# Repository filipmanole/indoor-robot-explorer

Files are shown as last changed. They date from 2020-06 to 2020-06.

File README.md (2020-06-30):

<!-- PROJECT SHIELDS -->
<!--
*** I'm using markdown "reference style" links for readability.
*** Reference links are enclosed in brackets [ ] instead of parentheses ( ).
*** See the bottom of this document for the declaration of the reference variables
*** for contributors-url, forks-url, etc. This is an optional, concise syntax you may use.
*** https://www.markdownguide.org/basic-syntax/#reference-style-links
-->

[][contributors-url]
[][forks-url]
[][stars-url]
[][issues-url]
[][linkedin-url]

<!-- PROJECT LOGO -->
<br />
<p align="center">

  <h1 align="center">Indoor Robot Explorer</h1>

  <p align="center">
    <a href="https://github.com/filipmanole/indoor-robot-explorer/issues">Report Bug</a>
    ·
    <a href="https://github.com/filipmanole/indoor-robot-explorer/issues">Request Feature</a>
  </p>
</p>

<!-- TABLE OF CONTENTS -->

## Table of Contents

- [About the Project](#about-the-project)
- [Software Tools](#software-tools)
- [Hardware](#hardware)
- [Getting Started](#getting-started)
  - [Prerequisites](#prerequisites)
  - [Usage](#usage)
- [Roadmap](#roadmap)
- [Contributing](#contributing)
- [License](#license)

<!-- ABOUT THE PROJECT -->

## About The Project

In recent years there has been an increase in interest in robots. There are billions of dollar spent on professional and personal use robots: autonomous vehicles, maintenance robots, cleaning robots. This repository offers a well structured, modular and low cost robot.

## Software Tools

Board layout was designed using [EAGLE 9.2.2](https://www.autodesk.com/products/eagle/overview?plc=F360&term=1-YEAR&support=ADVANCED&quantity=1)

Firmware was developed using:
- [MPLAB X 5.30](https://www.microchip.com/mplab/mplab-x-ide)
- dsPIC33E-GM-GP-MC-GU-MU_DFP 1.0.23
- [XC16](https://www.microchip.com/mplab/compilers) v1.50

Raspberry Pi specifications:
- [Raspbian GNU/Linux 9 (stretch)](https://www.raspberrypi.org/downloads/raspberry-pi-os/)
- [GCC](https://gcc.gnu.org/) version 6.3.0
- Python 2.7

## Hardware

### Main Components Used
- LiPo Battery 7V4 2200mA
- [dsPIC33EP128GM304](https://www.microchip.com/wwwproducts/en/dsPIC33EP128GM304) microcontroller
- 2x [MC33926](https://www.nxp.com/docs/en/data-sheet/MC33926.pdf) Motor Drivers
- 2x [Pololu ](https://www.pololu.com/product/2283) DC Motors
- 3x [VL53L0X]() Time of Flight Sensors
- [Raspberry Pi Zero W](https://www.raspberrypi.org/products/raspberry-pi-zero-w/)

In the `eagle_project` directory can be found the schematic, the layout design of the board and the Bill of Material. Those files can be used to send the board to manufacture and build the robot. You should obtain something like:

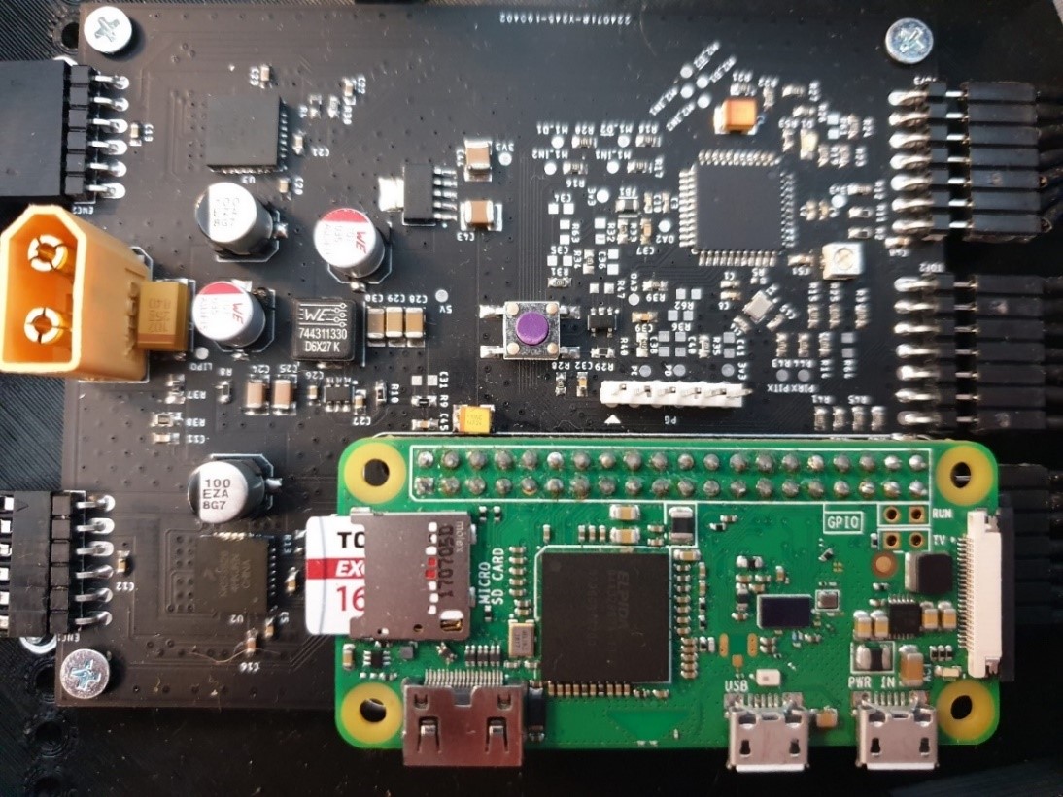
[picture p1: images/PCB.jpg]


<!-- GETTING STARTED -->

## Getting Started

To get a local copy up and running follow these simple example steps.

### Prerequisites

Make sure you have the following:
- The tools specified in [Software Tools](#software-tools) section
- The robot obtained from the files in the `eagle_project` directory
- [PICkit™ 3](https://www.microchip.com/DevelopmentTools/ProductDetails/PG164130) to programm the robot
- `ssh` connection to the Raspberry Pi Zero W.

```sh
git clone https://github.com/filipmanole/indoor-robot-explorer.git
```

<!-- USAGE EXAMPLES -->

### Usage

Program the robot:
1. Open the MPLAB X project `driver.X`
2. Right click on the project and select `Build`
3. Program the robot using the PICkit 3

Copy the directory `robot-utils` on the Raspberry Pi:
```sh
scp robot-utils/ pi_user@raspberry_pi_address:~
```
Log on the Raspberry Pi:
```sh
ssh pi_user@raspberry_pi_address
```
Run commands to move the robots:
```sh
cd ~/robot-utils/commands
make build
robot start        # robot can be controlled now
robot run 0.3 0.1  # first argument is the linear velocity, the second is the angular velocity
robot pose         # returns the position of the robot x, y and tetha
robot stop         # the robot stops
```

Example of how to get data from the sensors:
```sh
cd ~/robot-utils/tof/VL53L0X
python VL53L0X_multi_example.py
```

<!-- ROADMAP -->

## Roadmap

See the [open issues](https://github.com/filipmanole/indoor-robot-explorer/issues) for a list of proposed features (and known issues).

<!-- CONTRIBUTING -->

## Contributing

Contributions are what make the open source community such an amazing place to be learn, inspire, and create. Any contributions you make are **greatly appreciated**.

1. Fork the Project
2. Create your Feature Branch (`git checkout -b feature/AmazingFeature`)
3. Commit your Changes (`git commit -m 'Add some AmazingFeature'`)
4. Push to the Branch (`git push origin feature/AmazingFeature`)
5. Open a Pull Request

<!-- LICENSE -->

## License

Distributed under the MIT License.

<!-- CONTACT -->

<!-- ACKNOWLEDGEMENTS -->

<!-- MARKDOWN LINKS & IMAGES -->
<!-- https://www.markdownguide.org/basic-syntax/#reference-style-links -->

[contributors-shield]: https://img.shields.io/github/contributors/filipmanole/indoor-robot-explorer.svg?style=flat-square
[contributors-url]: https://github.com/filipmanole/indoor-robot-explorer/graphs/contributors
[forks-shield]: https://img.shields.io/github/forks/filipmanole/indoor-robot-explorer.svg?style=flat-square
[forks-url]: https://github.com/filipmanole/indoor-robot-explorer/network/members
[stars-shield]: https://img.shields.io/github/stars/filipmanole/indoor-robot-explorer.svg?style=flat-square
[stars-url]: https://github.com/filipmanole/indoor-robot-explorer/stargazers
[issues-shield]: https://img.shields.io/github/issues/filipmanole/indoor-robot-explorer.svg?style=flat-square
[issues-url]: https://github.com/filipmanole/indoor-robot-explorer/issues
[linkedin-shield]: https://img.shields.io/badge/-LinkedIn-black.svg?style=flat-square&logo=linkedin&colorB=555
[linkedin-url]: https://www.linkedin.com/in/filip-george-manole/
[product-screenshot]: screenshot.png

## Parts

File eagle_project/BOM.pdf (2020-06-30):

BILL OF MATERIALS

Qty | Value | Parts | MANUFACTURER_NAME | MANUFACTURER_PART_NUMBER
1 | | OA1 | Diodes Incorporated | TLV271CW5-7
1 | | S1 | E-Switch | LL3301NF065QG
1 | | FB1 | TDK | MPZ2012S102JTD25
1 | | D1 | Lite-On | LTST-C171GKT
2 | | U2, U3 | NXP / Freescale | MC33926PNB
1 | | P1 | Bourns | PVG3A203C01R00
1 | | U4 | Texas Instruments | TPS565201DDCT
1 | | J1 | SparkFun | PRT-10474
1 | | X1 | ECS | ECS-120-10-36-AGY-TR
1 | | U1 | Microchip Technology | dsPIC33EP128GM304-E/PT
1 | | U5 | Texas Instruments | TL1963A-33DCQR
3 | 0.1uF | C1, C2, C3 | | CC0402KRX7R7BB104

12 0.1uF

| | C6, C11, C12, C13, C21, C26, C27, C45, C48, C49, C50, C51 | | CC0603KRX7R9BB104
2 | 0.47uF | C7, C22 | | TMK107B7474KA-TR
7 | 100 | R6, R7, R28, R41, R42, R45, R46 | | AC0603FR-13100RL
2 | 100pF | C37, C39 | | 8.85342E+11
2 | 100uF | C33, C42 | Panasonic | EEH-ZA1E101XV
1 | 100uF | C17 | KEMET | T491X107M025AT
2 | 100uF | C18, C19 | Wurth Electronics | 865081000000
5 | 10k | R2, R8, R10, R11, R29 | | RC0402FR-0710KL
2 | 10uF | C24, C25 | | GRM188R6YA106MA73D
2 | 10uF | C43, C44 | | GRM32DR71E106MA12L
2 | 10uF | C4, C46 | | TAJB106K016TNJ
1 | 1M | R38 | | RC0603FR-071ML
4 | 1k | R1, R30, R31, R35 | | ERJ-3RBD102V
3 | 1nF | C8, C9, C10 | | AC0402KRX7R7BB102
1 | 1nF | C32 | | 885012000000
2 | 1uF | C16, C23 | | C1608X7R1V105K080AE
2 | 220 | R4, R13 | | UCR03EVPFLR220
2 | 22uF | C28, C29 | | EMK316BB7226ML-T
1 | 240 | R53 | | ERJ-3RBD2400V
1 | 2M | R37 | | RC0603FR-072ML
1 | 3.3uH | | L1 | Wurth Electronics | | 744311330
| | R3, R12, R14, R15, R16, R17,R18, R19, R20, R21, R22, R23, R24, R25, R26, R27, R43, R44 | | | RC0603FR-07330RL
2 | 33nF | | C5, C20 | | | CC0603KRX7R9BB333

18 330

4 | 4k3 | R33, R34, R39, R40 | AC0603FR-074K3L
2 | 4k7 | R65, R66 | SFR03EZPF4701
1 | 54k9 | R9 | ERJ-PB3B5492V
2 | 8pF | C14, C15 | GCM1555C1H8R0DA16D

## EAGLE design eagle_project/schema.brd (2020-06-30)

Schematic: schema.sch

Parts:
3V3, 3V3@2, 3V3@3, 3V3@4, 5V: TPB1,27; B1,27
C1, C2, C3: 0.1uF; C0402K; MANUFACTURER_PART_NUMBER CC0402KRX7R7BB104
C4, C46: 10uF; C1210K; MANUFACTURER_PART_NUMBER TAJB106K016TNJ
C5, C20: 33nF; C0603K; MANUFACTURER_PART_NUMBER CC0603KRX7R9BB333
C6, C11, C12, C13, C21, C26, C27, C45, C48, C49, C50, C51: 0.1uF; C0603K; MANUFACTURER_PART_NUMBER CC0603KRX7R9BB104
C7, C22: 0.47uF; C0603K; MANUFACTURER_PART_NUMBER TMK107B7474KA-TR
C8, C9, C10: 1nF; C0402K; MANUFACTURER_PART_NUMBER AC0402KRX7R7BB102
C14, C15: 8pF; C0402K; MANUFACTURER_PART_NUMBER GCM1555C1H8R0DA16D
C16, C23: 1uF; C0603K; MANUFACTURER_PART_NUMBER UMK107AB7105KA-T
C17: 100uF; CAPMP7141X430
C18, C19: 100uF; CAPAE660X770
C24, C25: 10uF; C1206K; MANUFACTURER_PART_NUMBER GMK316AB7106KL-TR
C28, C29: 22uF; C1206; MANUFACTURER_PART_NUMBER EMK316BB7226ML-T
C30: DNP; C1206
C31, C34, C35, C36, C38, C40, C41: DNP; C0603K
C32: 1nF; C0603K; MANUFACTURER_PART_NUMBER 885012206083
C33, C42: 100uF; CAPAE660X800
C37, C39: 100pF; C0603K; MANUFACTURER_PART_NUMBER 885342206001
C43, C44: 10uF; C1210K; MANUFACTURER_PART_NUMBER GRM32DR71E106MA12L
D1: LED0805; LEDC2012X80
ENC1, ENC2: 2283; 1X06/90
FB1: FERRITE_BEADS0805; BEADC2012X105
IC3: RASPBERRY_PI_ZERO_W_(V1.3)NO_HOLE; PI_0_W
J1: XT60
L1: 3.3uH; INDDFN700X690X400-2
LIPO: TPB1,27; B1,27
OA1: AMPLIFIERSOT25; SOT95P285X115-5
P1: POTENSIOMETER; PVG3A
PC: TPB1,27; B1,27
PD: TPB1,27; B1,27
PG: PICkit3; 1X06
PIRX: TPB1,27; B1,27
PITX: TPB1,27; B1,27
R1, R30, R31, R35: 1k; R0603; MANUFACTURER_PART_NUMBER ERJ-3RBD102V
R2, R8, R10, R11, R29: 10k; R0603; MANUFACTURER_PART_NUMBER ERJ-3RBD1002V
R3, R12, R14, R15, R16, R17, R18, R19, R20, R21, R22, R23, R24, R25, R26, R27, R43, R44: 330; R0603; MANUFACTURER_PART_NUMBER RC0603FR-07330RL
R4, R13: 220; R0603; MANUFACTURER_PART_NUMBER UCR03EVPFLR220
R5: DNP; R0402
R6, R7, R28, R41, R42, R45, R46: 100; R0603; MANUFACTURER_PART_NUMBER AC0603FR-13100RL
R9: 54k9; R0603; MANUFACTURER_PART_NUMBER ERJ-PB3B5492V
R32, R36, R47, R61, R62, R63, R64: DNP; R0603
R33, R34, R39, R40: 4k3; R0603; MANUFACTURER_PART_NUMBER AC0603FR-074K3L
R37: 2M; R0805; MANUFACTURER_PART_NUMBER ERJ-6RED2003V
R38: 1M; R0805; MANUFACTURER_PART_NUMBER AC0805FR-13100KL
R53: 240; R0603; MANUFACTURER_PART_NUMBER ERJ-3RBD2400V
R65, R66: 4k7; R0603; MANUFACTURER_PART_NUMBER SFR03EZPF4701
S1: BUTON_SPST; BUTON_SMD
TOF1, TOF2, TOF3: VL53L0X; 1X07/90
U1: DSPIC33EP128GM304TFQP44_WITH3D; QFP80P1200X1200X120-44
U2, U3: NXP_DRIVER; QFN80P800X800X220-33N
U4: TPS656201TPS565201; SOT95P280X110-6
U5: TL1963A-33DCQRDCQ; SOT127P706X180-6
U$1, U$2, U$3, U$4: MOUNTING_HOLE; HOLE_3.5MM
X1: XTALLECX; OSCCC250X200X60

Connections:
3V3: 3V3.TP, 3V3@2.TP, 3V3@3.TP, 3V3@4.TP, C1.2, C2.1, C8.2, C9.1, C44.1, C48.1, C49.1, C50.1, FB1.1, OA1.5 (VDD), P1.1 (3), PG.2, R2.2, R11.2, R29.1, R32.1, R36.1, R62.2, R63.2, R65.2, R66.2, TOF1.7, TOF2.7, TOF3.7, U1.28 (VDD), U1.40 (VDD), U5.4 (OUT), U5.5 (ADJ)
5V: 5V.TP, C12.2, C13.2, C19.1 (POSITIVE), C28.1, C29.1, C30.1, C31.1, C43.2, C45.2, C46.1, ENC1.3, ENC2.4, IC3.2 (+5V_1), IC3.4 (+5V_2), L1.2, R9.2, U5.1 (!SHDN), U5.2 (IN)
!MCLR: PG.1, R28.2, U1.18 (!MCLR)
GND: C1.1, C2.2, C3.1, C4.1, C6.1, C7.2, C8.1, C9.2, C10.1, C11.2, C12.1, C13.1, C14.1, C15.2, C16.2, C17.1 (NEGATIVE), C18.2 (NEGATIVE), C19.2 (NEGATIVE), C21.1, C22.2, C23.2, C24.2, C25.2, C26.2, C28.2, C29.2, C30.2, C32.2, C33.2 (NEGATIVE), C34.2, C36.2, C38.2, C41.2, C42.2 (NEGATIVE), C43.1, C44.2, C45.1, C46.2, C48.2, C49.2, C50.2, C51.2, D1.1 (-), ENC1.4, ENC2.3, IC3.6 (GND_1), IC3.9 (GND_2), IC3.14 (GND_3), IC3.20 (GND_4), IC3.25 (GND_5), IC3.30 (GND_6), IC3.34 (GND_7), IC3.39 (GND_8), J1.2 (-), OA1.2 (GND), P1.3 (1), PG.3, R4.1, R10.1, R13.1, R34.1, R38.2, R40.1, R61.1, R64.1, S1.1, S1.2, TOF1.5, TOF2.5, TOF3.5, U1.6 (VSS), U1.16 (AVSS), U1.29 (VSS), U1.39 (VSS), U2.5 (AGND), U2.17 (N.C.), U2.18 (PGND), U2.19 (PGND), U2.20 (PGND), U2.22 (PGND), U2.23 (PGND), U2.24 (PGND), U2.25 (N.C.), U2.33 (AGND), U3.5 (AGND), U3.17 (N.C.), U3.18 (PGND), U3.19 (PGND), U3.20 (PGND), U3.22 (PGND), U3.23 (PGND), U3.24 (PGND), U3.25 (N.C.), U3.33 (AGND), U4.1 (GND), U5.3 (GND), U5.6 (GND), U$1.P$1, U$2.P$1, U$3.P$1, U$4.P$1, X1.2 (GND), X1.4 (GND)
GPIO1: R7.2, TOF1.4
GPIO2: R46.2, TOF2.4
GPIO3: R42.2, TOF3.4
LIPO: C5.2, C6.2, C16.1, C17.2 (POSITIVE), C18.1 (POSITIVE), C20.2, C21.2, C23.1, C24.1, C25.1, C26.1, C33.1 (POSITIVE), C42.1 (POSITIVE), J1.1 (+), LIPO.TP, R8.2, R37.2, U2.4 (VPWR), U2.6 (VPWR), U2.11 (VPWR), U2.31 (VPWR), U3.4 (VPWR), U3.6 (VPWR), U3.11 (VPWR), U3.31 (VPWR), U4.3 (VIN)
LIPO_ADC: OA1.1 (OUT), OA1.4 (IN-), R47.1, U1.22 (RB1)
M1_!D2: R18.1, U1.12 (RA10)
M1_!SF: R3.1, U1.38 (RC5)
M1_D1: R20.2, U1.13 (RA7)
M1_EN: R25.1, U1.37 (RC4)
M1_FB: C7.1, C40.1, C41.1, R1.1, R35.1
M1_IN1: R17.2, U1.14 (RB14)
M1_IN2: R16.2, U1.15 (RB15)
M1_INV: R14.1, U1.36 (RC3)
M1_OUT1: ENC1.6, U2.12 (OUT1), U2.13 (OUT1), U2.14 (OUT1), U2.15 (OUT1)
M1_OUT2: ENC1.5, U2.27 (OUT2), U2.28 (OUT2), U2.29 (OUT2), U2.30 (OUT2)
M1_QEA: ENC1.2, U1.10 (RB12)
M1_QEB: ENC1.1, U1.11 (RB13)
M1_SLEW: R15.2, U1.35 (RA9)
M2_!D2: R26.1, U1.2 (RC6)
M2_!SF: R12.1, U1.41 (RB5)
M2_D1: R27.2, U1.3 (RC7)
M2_EN: R19.1, U1.44 (RB8)
M2_FB: C22.1, C34.1, C35.1, R30.1, R31.1
M2_IN1: R22.1, U1.4 (RC8)
M2_IN2: R21.1, U1.5 (RC9)
M2_INV: R24.1, U1.42 (RB6)
M2_OUT1: ENC2.2, U3.12 (OUT1), U3.13 (OUT1), U3.14 (OUT1), U3.15 (OUT1)
M2_OUT2: ENC2.1, U3.27 (OUT2), U3.28 (OUT2), U3.29 (OUT2), U3.30 (OUT2)
M2_QEA: ENC2.5, U1.8 (RB10)
M2_QEB: ENC2.6, U1.9 (RB11)
M2_SLEW: R23.1, U1.43 (RB7)
unnamed: R53.2, U1.1 (RB9)
unnamed: IC3.33 (GPIO13/PWM1), R41.1
unnamed: C27.2, U4.6 (VBST)
unnamed: C31.2, R9.1, R10.2, U4.4 (VFB)
unnamed: R14.2, U2.7 (INV)
unnamed: R21.2, U3.1 (IN2)
unnamed: R8.1, U4.5 (EN)
unnamed: R22.2, U3.2 (IN1)
unnamed: C4.2, U1.7 (VCAP)
unnamed: C27.1, L1.1, U4.2 (SW)
unnamed: R23.2, U3.3 (SLEW)
unnamed: R24.2, U3.7 (INV)
unnamed: R26.2, U3.16 (!D2)
unnamed: R27.1, U3.26 (D1)
unnamed: R20.1, U2.26 (D1)
unnamed: R16.1, U2.1 (IN2)
unnamed: R17.1, U2.2 (IN1)
unnamed: R15.1, U2.3 (SLEW)
unnamed: R18.2, U2.16 (!D2)
unnamed: R11.1, R12.2, U3.21 (!SF)
unnamed: IC3.35 (GPIO19/SPI0_MISO1/PWM1), R7.1
unnamed: R2.1, R3.2, U2.21 (!SF)
unnamed: R25.2, R64.2, U2.9 (N.C.), U2.10 (EN)
unnamed: R4.2, R30.2, U3.8 (FB)
unnamed: C5.1, U2.32 (CCP)
unnamed: R19.2, R61.2, U3.9 (N.C.), U3.10 (EN)
unnamed: IC3.36 (GPIO16/SPI1_CS2), R42.1
unnamed: IC3.37 (GPIO26), R6.1
unnamed: IC3.38 (GPIO20/SPI0_MOSI1), R45.1
unnamed: IC3.40 (GPIO21/SPI0_SCLK1), R46.1
unnamed: R1.2, R13.2, U2.8 (FB)
unnamed: C11.1, OA1.3 (IN+), R37.1, R38.1, R47.2
unnamed: IC3.8 (GPIO_14/[UART]_TXD0), PITX.TP, R43.2
unnamed: IC3.10 (GPIO_15/[UART]_RXD0), PIRX.TP, R44.2
unnamed: D1.2 (+), R53.1
unnamed: C3.2, C10.2, FB1.2, U1.17 (AVDD)
unnamed: C20.1, U3.32 (CCP)
OA2IN+: C35.2, R31.2, R63.1, U1.20 (RA1)
OA2IN-: C36.1, C37.2, R32.2, R33.1, R34.2, U1.21 (RB0)
OA2OUT: C37.1, R33.2, U1.19 (RA0)
OA3IN+: C40.2, R35.2, R62.1, U1.27 (RC2)
OA3IN-: C38.1, C39.2, R36.2, R39.1, R40.2, U1.26 (RC1)
OA3OUT: C39.1, R39.2, U1.25 (RC0)
OSC1: C14.2, R5.1, U1.30 (RA2), X1.3 (XTAL)
OSC2: C15.1, R5.2, U1.31 (RA3), X1.1 (XTAL)
PGEC: PC.TP, PG.5, U1.23 (RB2)
PGED: PD.TP, PG.4, U1.24 (RB3)
PI_RX: R44.1, U1.33 (RB4)
PI_TX: R43.1, U1.32 (RA8)
POT_ADC: C51.1, P1.2, U1.34 (RA4)
RESET: C32.1, R28.1, R29.2, S1.3, S1.4
SCL: IC3.5 (GPIO_3/[I2C]_SCL), R65.1, TOF1.2, TOF2.2, TOF3.2
SDA: IC3.3 (GPIO_2/[I2C]_SDA), R66.1, TOF1.1, TOF2.1, TOF3.1
XSHUT1: R6.2, TOF1.3
XSHUT2: R45.2, TOF2.3
XSHUT3: R41.2, TOF3.3

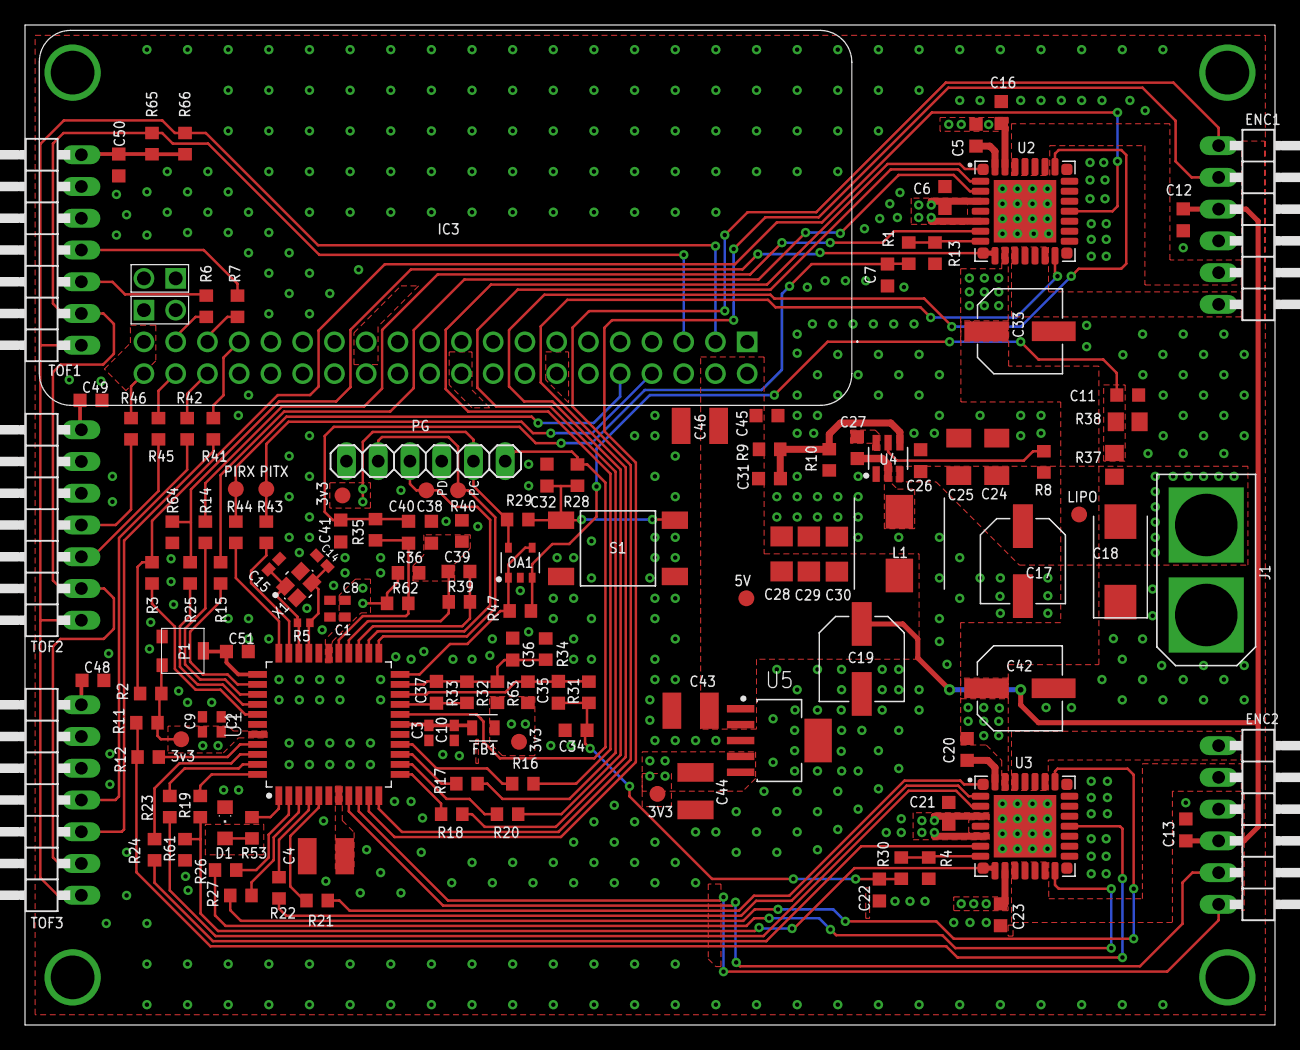
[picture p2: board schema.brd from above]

Board: 2 copper layers, 100.0 x 80.0 mm, 138 parts (0 on the bottom side), 91 nets.

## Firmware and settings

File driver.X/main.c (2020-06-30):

#include <stdio.h>
#include <string.h>
#include <libq.h>

#include <p33EP128GM304.h>
#define    FCY    35020800UL    // Instruction cycle frequency, Hz - required for __delayXXX() to work
#include <libpic30.h>        // __delayXXX() functions macros defined here

#include "mcc_generated_files/mcc.h"
#include "control.h"
#include "motor.h"

#define MY_BUFFER_SIZE  12

#define ACK             0x4D

uint8_t received_byte;

void STATE_init(void) {
    CONTROL_init();
    PWM_ModuleDisable();
    CONTROL_stop();
    CONTROL_setupPID();
    PWM4_SetExternalCallback(CONTROL_runPID);
}

void COMMAND_sendACK() {
    //UART1_Write(ACK);
    uint8_t ack = ACK;
    UART1_mySendBuffer(&ack, sizeof (ack));
}

bool COMMAND_recvACK(void) {
    uint8_t ack = 0;
    UART1_myRecvBuffer(&ack, sizeof (ack));
    
    if(ack == ACK) {
        return true;
    }
    
    return false;
}

void COMMAND_start(void) {
    CONTROL_start();
    CONTROL_clearHistory();
    PWM_ModuleEnable();
    
    /* Send ACK */
    COMMAND_sendACK();
}

void COMMAND_stop(void) {
    PWM_ModuleDisable();
    CONTROL_stop();
    
    /* Send ACK */
    COMMAND_sendACK();
}

void COMMAND_run(void) {
    int32_t received_v = 0;
    int32_t received_w = 0;

    uint8_t *recv_buff_v = &received_v;
    uint8_t *recv_buff_w = &received_w;

    UART1_myRecvBuffer(recv_buff_v, sizeof (received_v));
    UART1_myRecvBuffer(recv_buff_w, sizeof (received_w));

    
    //CONTROL_clearHistory();
    
    CONTROL_updateWheelsSpeed(received_v, received_w);
    
    /* Send ACK */
    COMMAND_sendACK();
}

void COMMAND_pose(void) {
    int32_t x = CONTROL_xGet();
    int32_t y = CONTROL_yGet();
    int32_t fi = CONTROL_fiGet();

    uint8_t *send_x = &x;
    uint8_t *send_y = &y;
    uint8_t *send_fi = &fi;
    
    UART1_mySendBuffer(send_x, sizeof (x));
    UART1_mySendBuffer(send_y, sizeof (y));
    UART1_mySendBuffer(send_fi, sizeof (fi));

    /* Recv ACK */
    COMMAND_recvACK();
}

void COMMAND_vel(void) {
    int32_t vr = CONTROL_vrGet();
    int32_t vl = CONTROL_vlGet();

    uint8_t *send_vr = &vr;
    uint8_t *send_vl = &vl;

    UART1_mySendBuffer(send_vr, sizeof (vr));
    UART1_mySendBuffer(send_vl, sizeof (vl));
    
    /* Recv ACK */
    COMMAND_recvACK();
}

void COMMAND_recv_vel(void) {
    int32_t received_vr = 0;
    int32_t received_vl = 0;

    uint8_t *recv_buff_vr = &received_vr;
    uint8_t *recv_buff_vl = &received_vl;

    UART1_myRecvBuffer(recv_buff_vr, sizeof (received_vr));
    UART1_myRecvBuffer(recv_buff_vl, sizeof (received_vl));
    
    CONTROL_vrSet(received_vr);
    CONTROL_vlSet(received_vl);
    
    CONTROL_updatePose(received_vr, received_vl);
    
    /* Send ACK */
    COMMAND_sendACK();
    
//    int16_t vrf = received_vr / 65536;
//    int16_t vlf = received_vl / 65536;
//    CONTROL_updatePoseFloat(vrf, vlf);
}

void (*COMMANDS[6])() = {   
                            COMMAND_stop, 
                            COMMAND_start, 
                            COMMAND_run,
                            COMMAND_pose, 
                            COMMAND_vel,
                            COMMAND_recv_vel
                        };

int main(void) {
    
    SYSTEM_Initialize();
    STATE_init();

    while (1) {
        if (!UART1_ReceiveBufferIsEmpty()) {
            //received_byte = UART1_Read();
            UART1_myRecvBuffer(&received_byte, sizeof (received_byte));
            LED_Toggle();
            COMMANDS[received_byte]();
        }
    }

    return 1;
}

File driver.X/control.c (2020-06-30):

#include "control.h"
#include <dsp.h>
#include <stdio.h>
#include <libpic30.h>
#include <string.h>
#include "mcc_generated_files/mcc.h"
#include "motor.h"
#include <math.h>

#define L               _Q16ftoi(0.17)          /* distance between the wheels  */
#define R               _Q16ftoi(0.03)          /* radius of the wheels         */
#define N               _Q16ftoi(48 * 20.4)     /* Counts per revolution        */

#define _2piRoverN      _Q16ftoi(0.00019249954) /* 2 * PI * R / N               */
#define _Nover2pi       _Q16ftoi(155.844520276) /* N / (2 * PI)                 */

#define _pi_q16         _Q16ftoi(PI)            /* PI                           */
#define _2pi_q16        _Q16ftoi(2 * PI)        /* 2 * PI                       */

#define MAX_VEL         60                      /* Maximum velocity for a wheel */

volatile tPID leftPID, rightPID;

volatile fractional abcCoefficientLeft[3] __attribute__ ((section (".xbss, bss, xmemory")));
volatile fractional controlHistoryLeft[3] __attribute__ ((section (".ybss, bss, ymemory")));
volatile fractional kCoeffsLeft[] = {0,0,0};

volatile fractional abcCoefficientRight[3] __attribute__ ((section (".xbss, bss, xmemory")));
volatile fractional controlHistoryRight[3] __attribute__ ((section (".ybss, bss, ymemory")));
volatile fractional kCoeffsRight[] = {0,0,0};

volatile _Q16 vr, vl;
volatile _Q16 x, y, fi;

void CONTROL_init(void)
{
    MOTOR_rightInit();
    MOTOR_leftInit();
}

void CONTROL_start(void)
{
    MOTOR_rightEnable();
    MOTOR_leftEnable();
}

void CONTROL_stop(void)
{
    MOTOR_rightDisable();
    MOTOR_leftDisable();
}

int32_t CONTROL_xGet(void)
{
    return x;
}

int32_t CONTROL_yGet(void)
{
    return y;
}

int32_t CONTROL_fiGet(void)
{
    return fi;
}

int32_t CONTROL_vlGet(void)
{
    return vl;
}

int32_t CONTROL_vrGet(void)
{
    return vr;
}

void CONTROL_vlSet(_Q16 new_vl)
{
    vl = new_vl;
}

void CONTROL_vrSet(_Q16 new_vr)
{
    vr = new_vr;
}

void CONTROL_setLeftPidCoeffs(fractional Kp, fractional Ki, fractional Kd)
{
    kCoeffsLeft[0] = Kp;
    kCoeffsLeft[1] = Ki;
    kCoeffsLeft[2] = Kd;
}

void CONTROL_setRightPidCoeffs(fractional Kp, fractional Ki, fractional Kd)
{
    kCoeffsRight[0] = Kp;
    kCoeffsRight[1] = Ki;
    kCoeffsRight[2] = Kd;
}

void CONTROL_setupPID(void)
{
    /* Set up pointer to derived coefficients */
    rightPID.abcCoefficients = &abcCoefficientRight[0];
    leftPID.abcCoefficients = &abcCoefficientLeft[0];
    
    
    /* Set up pointer to controller history samples */
    rightPID.controlHistory = &controlHistoryRight[0];
    leftPID.controlHistory = &controlHistoryLeft[0];
    
    /* Clear the controller history and the controller output */
    PIDInit(&rightPID);
    PIDInit(&leftPID);

    /* Derive the a,b, & c coefficients from the Kp, Ki & Kd */
    CONTROL_setRightPidCoeffs(Q15(0.6), Q15(0.15), Q15(0.0));
    CONTROL_setLeftPidCoeffs(Q15(0.6), Q15(0.15), Q15(0.0));
    
    PIDCoeffCalc(&kCoeffsRight[0], &rightPID);
    PIDCoeffCalc(&kCoeffsLeft[0], &leftPID);   
}

_Q16 angle_norm(_Q16 angle){
	_Q16 new_angle = angle;
    
    _Q16 k = abs(_Q16div(new_angle, _2pi_q16));
    k = k >> 16;
    k = k << 16;
    
    if(new_angle <= 0) {
        k = -k;
    }
        
    new_angle = new_angle - _Q16mpy(k, _2pi_q16);
    if(new_angle < -_pi_q16){
        new_angle = new_angle + _2pi_q16;
    }
    if(new_angle > _pi_q16){
        new_angle = new_angle - _2pi_q16;
    }
    
    return new_angle;
}

void CONTROL_updatePose(_Q16 vel_right, _Q16 vel_left)
{
    /* The result is multiplied with the sign of the velocity */
    _Q16 Dr = _Q16mpy(_2piRoverN, vel_right);
    _Q16 Dl = _Q16mpy(_2piRoverN, vel_left);
    
    _Q16 Dc = _Q16div(Dr + Dl, _Q16ftoi(2.0));
    
    x = x + _Q16mpy(Dc, _Q16cos(fi));
    y = y + _Q16mpy(Dc, _Q16sin(fi));
    fi = fi + _Q16div(Dr - Dl, L);
    
    fi = angle_norm(fi);
}

void CONTROL_runPID(void)
{
    /* Setting control reference */
    rightPID.controlReference = Q15(_itofQ16(_Q16div(vr, _Q16ftoi(MAX_VEL))));
    leftPID.controlReference = Q15(_itofQ16(_Q16div(vl, _Q16ftoi(MAX_VEL))));
    
    /* Running PID */
    PID(&rightPID);
    PID(&leftPID);
    
    /* Reading the current velocity */
    int16_t vel2 = VEL2CNT;
    int16_t vel1 = VEL1CNT;
    
    _Q16 vel2_Q16 = _Q16ftoi(abs(vel2));
    _Q16 vel1_Q16 = _Q16ftoi(abs(vel1));
    
    /* Setting the measured output to current velocity */
    rightPID.measuredOutput = Q15(_itofQ16(_Q16div(vel2_Q16, _Q16ftoi(MAX_VEL))));
    leftPID.measuredOutput = Q15(_itofQ16(_Q16div(vel1_Q16, _Q16ftoi(MAX_VEL))));
    
    /* Scaling the control output */
    uint16_t result2 = _itofQ16(_Q16mpy(_Q16ftoi(Fract2Float(rightPID.controlOutput)), _Q16ftoi(0xDB7)));
    uint16_t result1 = _itofQ16(_Q16mpy(_Q16ftoi(Fract2Float(leftPID.controlOutput)), _Q16ftoi(0xDB7)));
    
    /* Setting the new duty cycle */
    PWM_DutyCycleSet(PWM_GENERATOR_4, result2);
    PWM_DutyCycleSet(PWM_GENERATOR_6, result1);
    
    /* Updating robot POSE */
    CONTROL_updatePose(_Q16ftoi(-vel2), _Q16ftoi(vel1));
}

void CONTROL_updateWheelsSpeed(_Q16 v, _Q16 w)
{
    _Q16 VMAX = _Q16ftoi(15);
    _Q16 rotation = _Q16mpy(w, _Q16div(L, R));
    _Q16 translation = _Q16div(v, R);
    
    _Q16 aux_vr = _Q16mpy(translation + rotation, _Nover2pi);
    _Q16 aux_vl = _Q16mpy(translation - rotation, _Nover2pi);
    
    if(aux_vl > VMAX)
    {
        aux_vr = _Q16div(_Q16mpy(aux_vr, VMAX), aux_vl);
        aux_vl = VMAX;
    }
    
    if(aux_vr > VMAX)
    {
        aux_vl = _Q16div(_Q16mpy(aux_vl, VMAX), aux_vr);
        aux_vr = VMAX;
    }
    
    IFS6bits.PWM4IF = false;
    IFS6bits.PWM6IF = false;
    
    IEC6bits.PWM4IE = false;
    IEC6bits.PWM6IE = false;
    
    
    //IEC0bits.U1RXIE = 0;
    
    CONTROL_clearHistory();
    
    if(aux_vr > 0)
    {
        MOTOR_rightForward();
        vr = aux_vr;
    }
    else
    {
        MOTOR_rightBackward();
        vr = -aux_vr;
    }
    
    if(aux_vl > 0)
    {
        MOTOR_leftForward();
        vl = aux_vl;
    }
    else
    {
        MOTOR_leftBackward();
        vl = -aux_vl;
    }
    
    IFS6bits.PWM4IF = true;
    IFS6bits.PWM6IF = true;
    
    IEC6bits.PWM4IE = true;
    IEC6bits.PWM6IE = true;
    
    //IEC0bits.U1RXIE = 1;
}

void CONTROL_clearHistory(void) {
    leftPID.controlHistory[0] = 0;
    leftPID.controlHistory[1] = 0;
    leftPID.controlHistory[2] = 0;
    rightPID.controlHistory[0] = 0;
    rightPID.controlHistory[1] = 0;
    rightPID.controlHistory[2] = 0;
}

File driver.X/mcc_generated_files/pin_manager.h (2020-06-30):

/**
  PIN MANAGER Generated Driver File

  @Company:
    Microchip Technology Inc.

  @File Name:
    pin_manager.h

  @Summary:
    This is the generated manager file for the PIC24 / dsPIC33 / PIC32MM MCUs device.  This manager
    configures the pins direction, initial state, analog setting.
    The peripheral pin select, PPS, configuration is also handled by this manager.

  @Description:
    This source file provides implementations for PIN MANAGER.
    Generation Information :
        Product Revision  :  PIC24 / dsPIC33 / PIC32MM MCUs - 1.95-b-SNAPSHOT
        Device            :  dsPIC33EP128GM304
    The generated drivers are tested against the following:
        Compiler          :  XC16 v1.36
        MPLAB 	          :  MPLAB X v5.10
*/

/*
    (c) 2016 Microchip Technology Inc. and its subsidiaries. You may use this
    software and any derivatives exclusively with Microchip products.

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
    IN NO EVENT WILL MICROCHIP BE LIABLE FOR ANY INDIRECT, SPECIAL, PUNITIVE,
    INCIDENTAL OR CONSEQUENTIAL LOSS, DAMAGE, COST OR EXPENSE OF ANY KIND
    WHATSOEVER RELATED TO THE SOFTWARE, HOWEVER CAUSED, EVEN IF MICROCHIP HAS
    BEEN ADVISED OF THE POSSIBILITY OR THE DAMAGES ARE FORESEEABLE. TO THE
    FULLEST EXTENT ALLOWED BY LAW, MICROCHIP'S TOTAL LIABILITY ON ALL CLAIMS IN
    ANY WAY RELATED TO THIS SOFTWARE WILL NOT EXCEED THE AMOUNT OF FEES, IF ANY,
    THAT YOU HAVE PAID DIRECTLY TO MICROCHIP FOR THIS SOFTWARE.

    MICROCHIP PROVIDES THIS SOFTWARE CONDITIONALLY UPON YOUR ACCEPTANCE OF THESE
    TERMS.
*/

#ifndef _PIN_MANAGER_H
#define _PIN_MANAGER_H
/**
    Section: Includes
*/
#include <xc.h>

/**
    Section: Device Pin Macros
*/
/**
  @Summary
    Sets the GPIO pin, RA3, high using LATA3.

  @Description
    Sets the GPIO pin, RA3, high using LATA3.

  @Preconditions
    The RA3 must be set to an output.

  @Returns
    None.

  @Param
    None.

  @Example
    <code>
    // Set RA3 high (1)
    test_SetHigh();
    </code>

*/
#define test_SetHigh()          _LATA3 = 1
/**
  @Summary
    Sets the GPIO pin, RA3, low using LATA3.

  @Description
    Sets the GPIO pin, RA3, low using LATA3.

  @Preconditions
    The RA3 must be set to an output.

  @Returns
    None.

  @Param
    None.

  @Example
    <code>
    // Set RA3 low (0)
    test_SetLow();
    </code>

*/
#define test_SetLow()           _LATA3 = 0
/**
  @Summary
    Toggles the GPIO pin, RA3, using LATA3.

  @Description
    Toggles the GPIO pin, RA3, using LATA3.

  @Preconditions
    The RA3 must be set to an output.

  @Returns
    None.

  @Param
    None.

  @Example
    <code>
    // Toggle RA3
    test_Toggle();
    </code>

*/
#define test_Toggle()           _LATA3 ^= 1
/**
  @Summary
    Reads the value of the GPIO pin, RA3.

  @Description
    Reads the value of the GPIO pin, RA3.

  @Preconditions
    None.

  @Returns
    None.

  @Param
    None.

  @Example
    <code>
    uint16_t portValue;

    // Read RA3
    postValue = test_GetValue();
    </code>

*/
#define test_GetValue()         _RA3
/**
  @Summary
    Configures the GPIO pin, RA3, as an input.

  @Description
    Configures the GPIO pin, RA3, as an input.

  @Preconditions
    None.

  @Returns
    None.

  @Param
    None.

  @Example
    <code>
    // Sets the RA3 as an input
    test_SetDigitalInput();
    </code>

*/
#define test_SetDigitalInput()  _TRISA3 = 1
/**
  @Summary
    Configures the GPIO pin, RA3, as an output.

  @Description
    Configures the GPIO pin, RA3, as an output.

  @Preconditions
    None.

  @Returns
    None.

  @Param
    None.

  @Example
    <code>
    // Sets the RA3 as an output
    test_SetDigitalOutput();
    </code>

*/
#define test_SetDigitalOutput() _TRISA3 = 0
/**
  @Summary
    Sets the GPIO pin, RA7, high using LATA7.

  @Description
    Sets the GPIO pin, RA7, high using LATA7.

  @Preconditions
    The RA7 must be set to an output.

  @Returns
    None.

  @Param
    None.

  @Example
    <code>
    // Set RA7 high (1)
    M1_D1_SetHigh();
    </code>

*/
#define M1_D1_SetHigh()          _LATA7 = 1
/**
  @Summary
    Sets the GPIO pin, RA7, low using LATA7.

  @Description
    Sets the GPIO pin, RA7, low using LATA7.

  @Preconditions
    The RA7 must be set to an output.

  @Returns
    None.

  @Param
    None.

  @Example
    <code>
    // Set RA7 low (0)
    M1_D1_SetLow();
    </code>

*/
#define M1_D1_SetLow()           _LATA7 = 0
/**
  @Summary
    Toggles the GPIO pin, RA7, using LATA7.

  @Description
    Toggles the GPIO pin, RA7, using LATA7.

  @Preconditions
    The RA7 must be set to an output.

  @Returns
    None.

  @Param
    None.

  @Example
    <code>
    // Toggle RA7
    M1_D1_Toggle();
    </code>

*/
#define M1_D1_Toggle()           _LATA7 ^= 1
/**
  @Summary
    Reads the value of the GPIO pin, RA7.

  @Description
    Reads the value of the GPIO pin, RA7.

  @Preconditions
    None.

  @Returns
    None.

  @Param
    None.

  @Example
    <code>
    uint16_t portValue;

    // Read RA7
    postValue = M1_D1_GetValue();
    </code>

*/
#define M1_D1_GetValue()         _RA7
/**
  @Summary
    Configures the GPIO pin, RA7, as an input.

  @Description
    Configures the GPIO pin, RA7, as an input.

  @Preconditions
    None.

  @Returns
    None.

  @Param
    None.

  @Example
    <code>
    // Sets the RA7 as an input
    M1_D1_SetDigitalInput();
    </code>

*/
#define M1_D1_SetDigitalInput()  _TRISA7 = 1
/**
  @Summary
    Configures the GPIO pin, RA7, as an output.

  @Description
    Configures the GPIO pin, RA7, as an output.

  @Preconditions
    None.

  @Returns
    None.

  @Param
    None.

  @Example
    <code>
    // Sets the RA7 as an output
    M1_D1_SetDigitalOutput();
    </code>

*/
#define M1_D1_SetDigitalOutput() _TRISA7 = 0
/**
  @Summary
    Sets the GPIO pin, RA9, high using LATA9.

  @Description
    Sets the GPIO pin, RA9, high using LATA9.

  @Preconditions
    The RA9 must be set to an output.

  @Returns
    None.

  @Param
    None.

  @Example
    <code>
    // Set RA9 high (1)
    M1_SLEW_SetHigh();
    </code>

*/
#define M1_SLEW_SetHigh()          _LATA9 = 1
/**
  @Summary
    Sets the GPIO pin, RA9, low using LATA9.

  @Description
    Sets the GPIO pin, RA9, low using LATA9.

  @Preconditions
    The RA9 must be set to an output.

  @Returns
    None.

  @Param
    None.

  @Example
    <code>
    // Set RA9 low (0)
    M1_SLEW_SetLow();
    </code>

*/
#define M1_SLEW_SetLow()           _LATA9 = 0
/**
  @Summary
    Toggles the GPIO pin, RA9, using LATA9.

  @Description
    Toggles the GPIO pin, RA9, using LATA9.

  @Preconditions
    The RA9 must be set to an output.

  @Returns
    None.

  @Param
    None.

  @Example
    <code>
    // Toggle RA9
    M1_SLEW_Toggle();
    </code>
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

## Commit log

2020-06-30 added schematic and layout;added driver implementation
    [schema.brd, schema.sch]
2020-06-30 updated readme; added BOM; added robot-utils
    [schema.brd, schema.sch]
